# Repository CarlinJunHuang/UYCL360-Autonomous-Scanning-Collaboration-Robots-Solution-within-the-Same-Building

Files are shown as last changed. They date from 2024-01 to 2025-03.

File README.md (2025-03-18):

# Autonomous Scanning Collaboration Solution within the Same Building

## SDIM Group 3 - Fall 2023 at Southern University of Science and Technology

We are Group 3 from the School of System Design and Intelligent Manufacturing (SDIM) during the Fall 2023 semester at Southern University of Science and Technology. We have proposed an autonomous scanning solution designed for collaborative operation within the same building. This solution is aimed at alleviating the physical labor burden of technical workers in construction site measurement and quantification tasks.

### Design and Functionality

Explore more on my personal website: https://huangjuncarlin.me/hero-works/uycl360

In terms of appearance, we have conducted Kansei Engineering measurements and established engineering features to create a design that meets the enterprise's demands for a sense of technology and reliability. Functionally, we have broken down the requirements into four aspects: movement, scanning, scheduling, and management. We have implemented various technical solutions, including:

- A screw rail scanner lifting mechanism
- Ultra-wideband wireless communication for centimeter-level machine positioning
- UWB feedback control for following the operator's movement
- Dual-loop motion control with PID for speed and position
- Part simulation and optimization using Abaqus
- APP and physical controller design compliant with ergonomics

For a detailed overview, please refer to our key selling points image below:
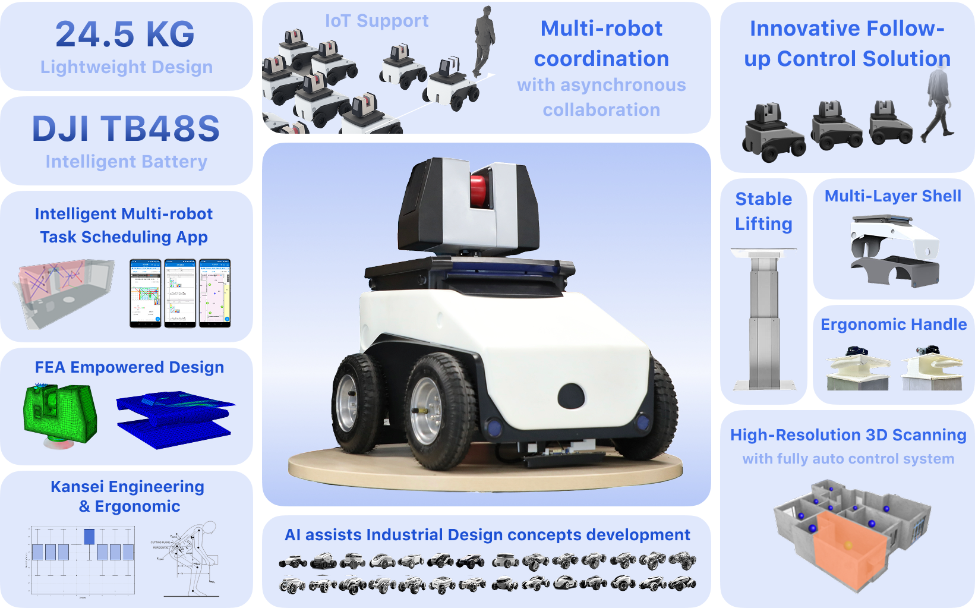
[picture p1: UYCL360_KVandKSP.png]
Key Selling Points


### Open Source Commitment

We are committed to open-sourcing as many of the technologies and techniques we have applied as possible, with the hope of aiding your learning journey. 
However, please note that some documentation may involve third-party commercial copyrights, and we will upload such material after proper anonymization and consideration.

By the way, in most cases our source text or files in this repository are in Chinese. But we will try our best to translate those parts into English via DeepL or Google Translate.

### How You Can Contribute

If you find this useful, please give us a Star or let us know! Should you have any questions, feel free to ask us.

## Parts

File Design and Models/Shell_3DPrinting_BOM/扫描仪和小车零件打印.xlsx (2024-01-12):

扫描仪+小车车壳 打样需求
序号 | 物料名称（STL文件名） | 图片 | 数量 | 样色
1 | 扫描仪-最左侧黑壳.STL |  | 1
2 | 扫描仪-左中侧灰壳.STL |  | 1
3 | 扫描仪-中间黑-红-黑部件.STL |  | 1
4 | 扫描仪-右中侧灰壳.STL |  | 1
5 | 扫描仪-最右侧黑壳.STL |  | 1
6 | 小车-外壳顶.STL |  | 1
7 | 小车-外壳中.STL |  | 1
8 | 小车-外壳底.STL |  | 1

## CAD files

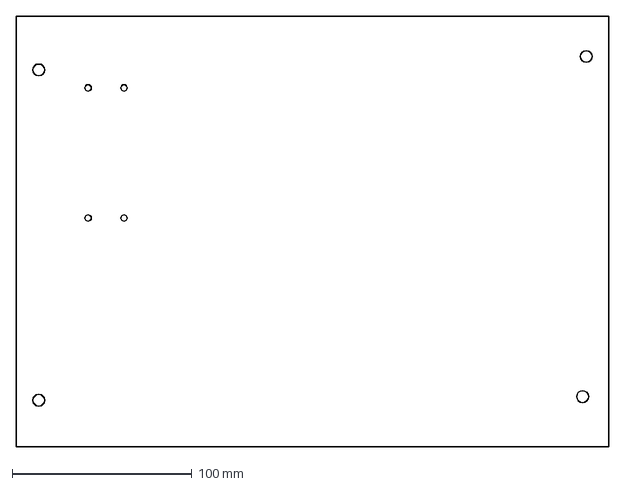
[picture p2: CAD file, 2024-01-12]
Chassis basics/Chassis Model/板V3.DXF
330.0 x 240.0 mm

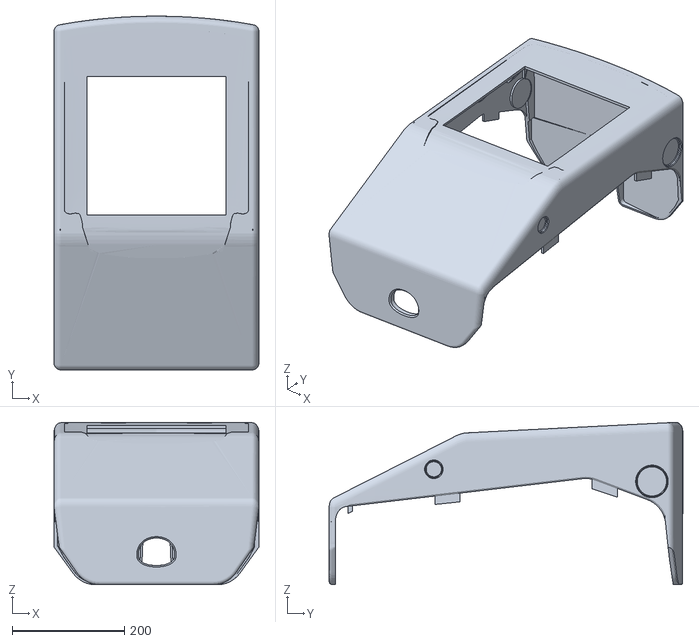
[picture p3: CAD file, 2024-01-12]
Design and Models/Shell_3DPrinting_BOM/小车-外壳中.STL
365.1 x 629.9 x 289.3

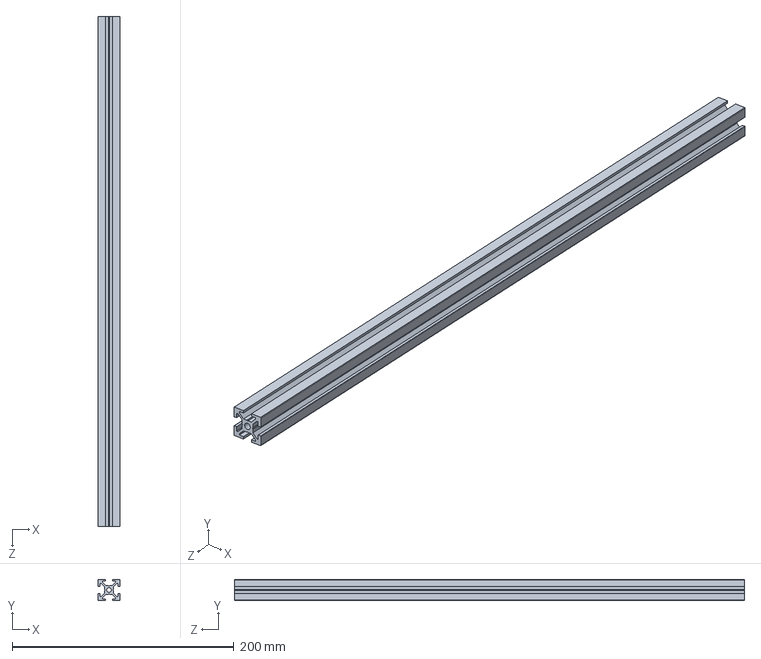
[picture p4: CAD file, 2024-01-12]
Chassis basics/Chassis Model/底盘横梁（4根）.SLDPRT
20.0 x 19.2 x 460.0 mm

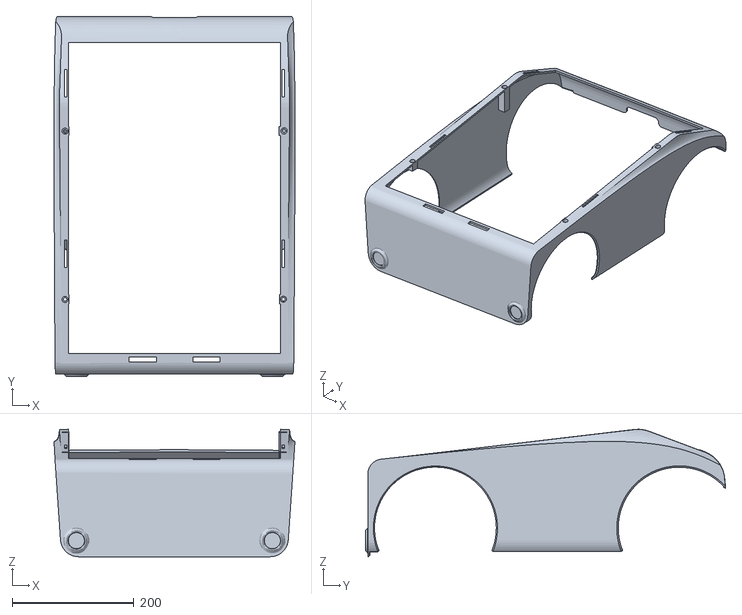
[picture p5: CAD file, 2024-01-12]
Design and Models/Shell_3DPrinting_BOM/小车-外壳底.STL
395.9 x 591.9 x 209.5

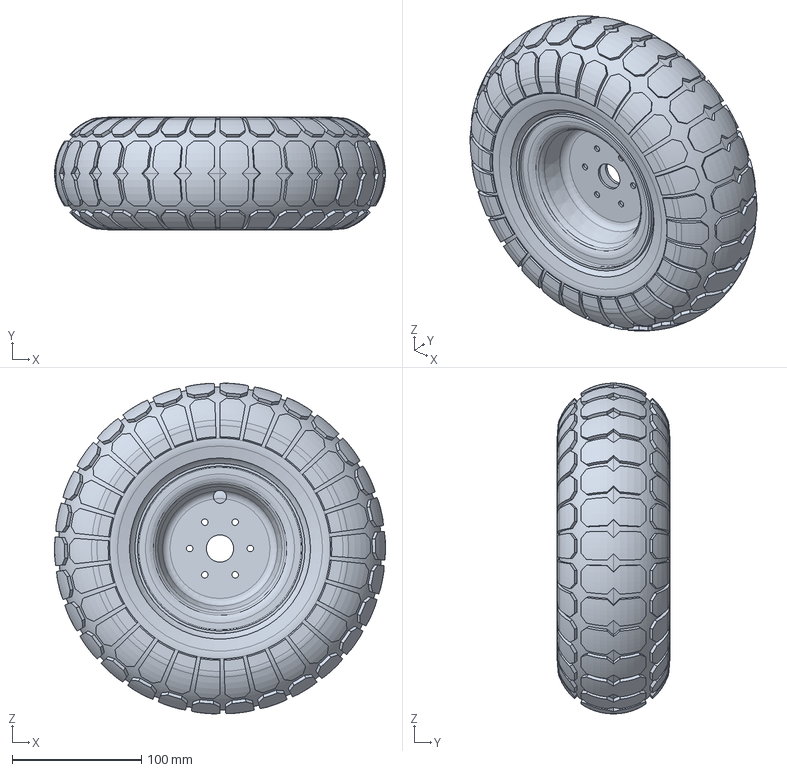
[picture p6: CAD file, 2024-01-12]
Chassis basics/Chassis Model/充气轮_10寸(直径256mm）.stp
256.0 x 87.1 x 255.8 mm

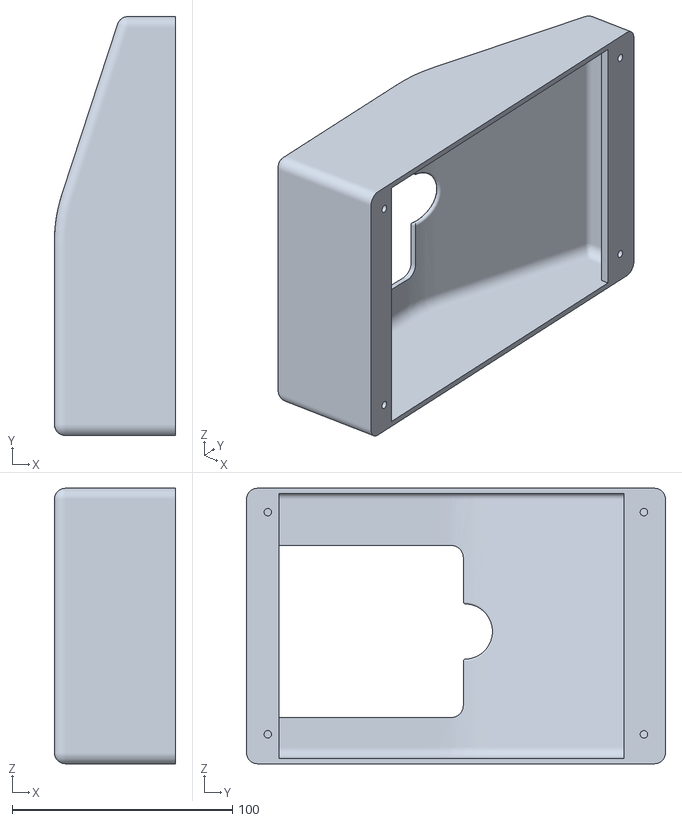
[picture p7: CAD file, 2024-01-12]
Design and Models/Shell_3DPrinting_BOM/扫描仪-最左侧黑壳.STL
55.0 x 190.0 x 125.0

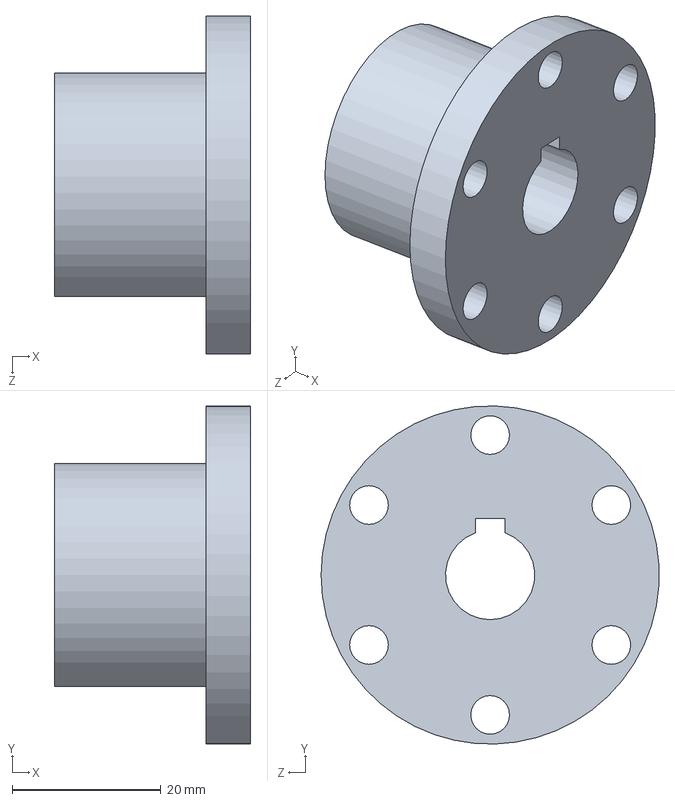
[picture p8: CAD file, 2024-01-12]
Chassis basics/Chassis Model/轮胎联轴器.SLDPRT
26.4 x 45.4 x 45.4 mm

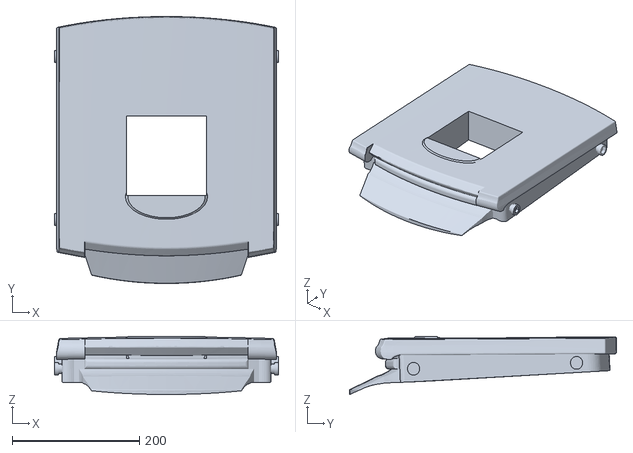
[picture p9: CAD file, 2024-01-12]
Design and Models/Shell_3DPrinting_BOM/小车-外壳顶.STL
352.1 x 419.5 x 91.2

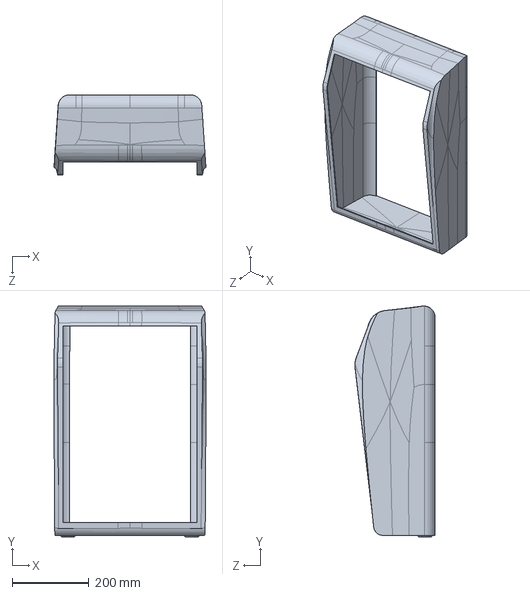
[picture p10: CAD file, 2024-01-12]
Chassis basics/Chassis Model/不知道该不该死10底.SLDPRT
395.9 x 601.8 x 209.5 mm

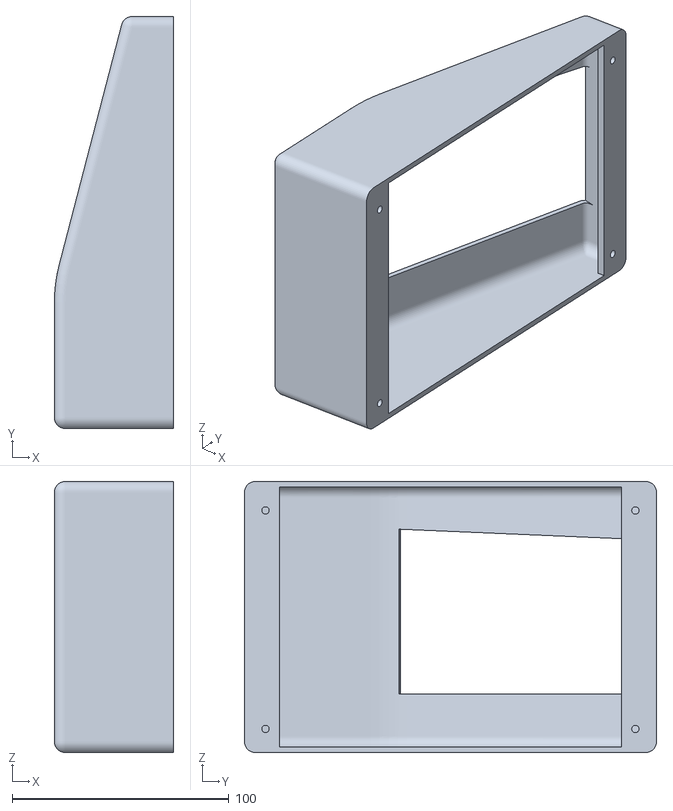
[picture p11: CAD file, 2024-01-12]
Design and Models/Shell_3DPrinting_BOM/扫描仪-最右侧黑壳.STL
55.0 x 190.0 x 125.0

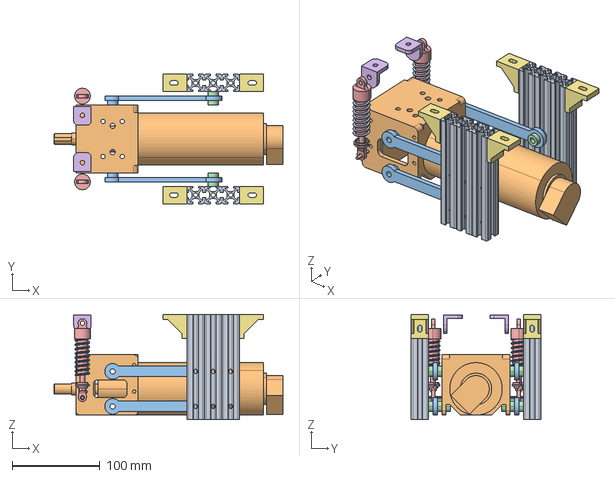
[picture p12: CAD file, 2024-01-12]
Chassis basics/Chassis Model/MD60独立悬挂.stp
261.5 x 148.0 x 120.0 mm

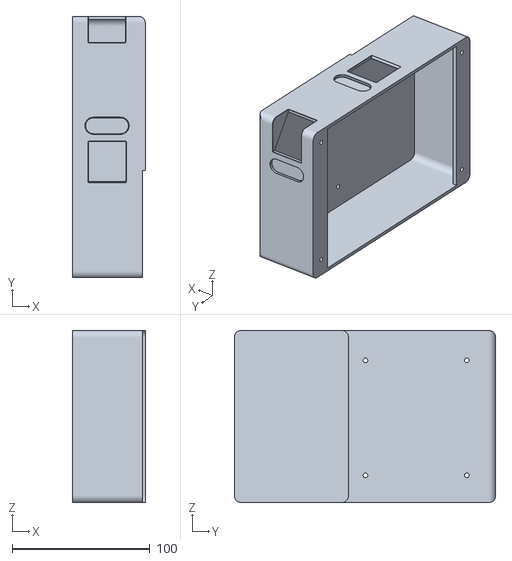
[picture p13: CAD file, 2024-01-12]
Design and Models/Shell_3DPrinting_BOM/扫描仪-左中侧灰壳.STL
52.9 x 190.0 x 125.0

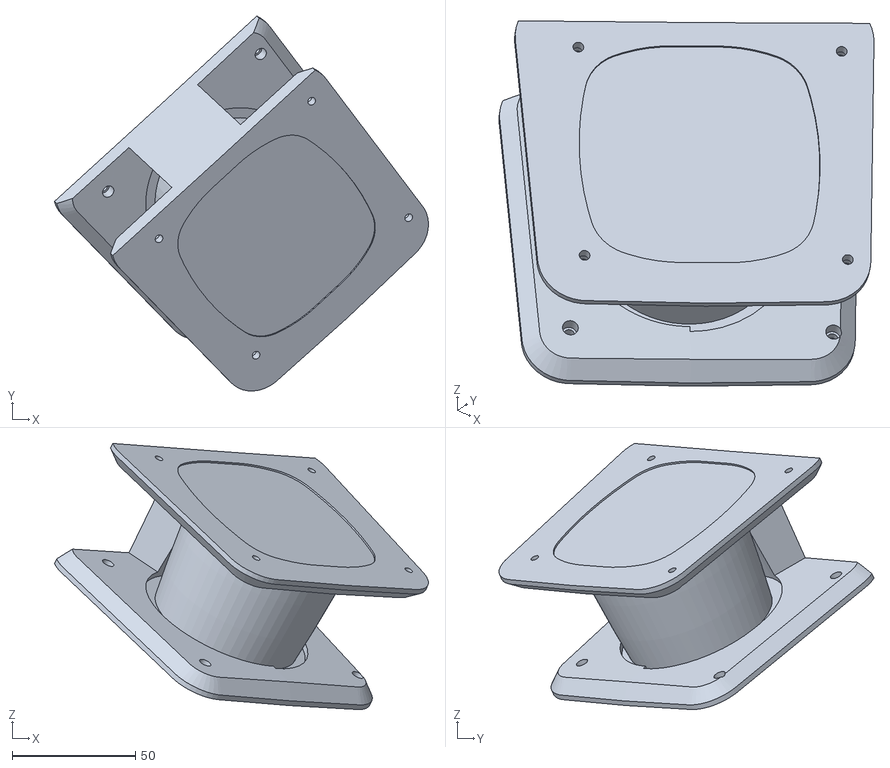
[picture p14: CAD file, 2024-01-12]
Design and Models/Shell_3DPrinting_BOM/扫描仪-中间黑-红-黑部件.STL
151.9 x 152.3 x 108.1

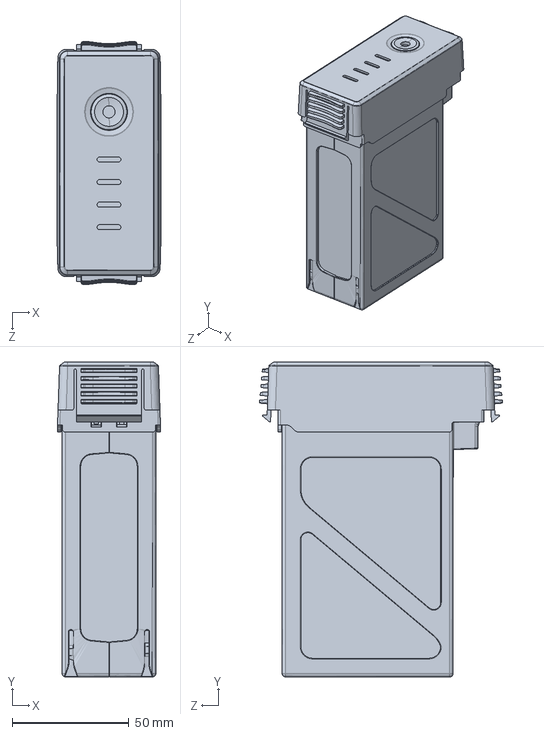
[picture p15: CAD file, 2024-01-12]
Chassis basics/Chassis Model/TB47S电池官网.SLDPRT
44.3 x 134.8 x 103.9 mm

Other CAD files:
Chassis basics/Chassis Model/2020型材截面.SLDPRT
Design and Models/Shell_3DPrinting_BOM/扫描仪-右中侧灰壳.STL
Chassis basics/Chassis Model/型材截面2020.dxf
Chassis basics/Chassis Model/板V1.SLDPRT
Chassis basics/Chassis Model/MD60轮组模块.stp
Chassis basics/Chassis Model/_MD60________^MD60独立悬挂.stp.SLDPRT
Chassis basics/Chassis Model/底盘纵梁（2根）.SLDPRT
Chassis basics/Chassis Model/板V1.DXF
Chassis basics/Chassis Model/板V2.DXF

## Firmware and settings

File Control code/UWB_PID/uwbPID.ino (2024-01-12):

//#include <SimpleKalmanFilter.h>

#define LED PC13                    //调试用的LED

//以下为左前方电机引脚定义
#define LF_Motor_IN1 PA5            //LF电机使能引脚1
#define LF_Motor_IN2 PA4            //LF电机使能引脚2
#define LF_PWM PA0                  //LF电机调速引脚
#define LF_ENCODER_A PB6            //LF编码器A相引脚
#define LF_ENCODER_B PB7            //LF编码器B相引脚

//以下为右前方电机引脚定义
#define RF_Motor_IN1 PB0            //RF电机使能引脚1
#define RF_Motor_IN2 PB1            //RF电机使能引脚2
#define RF_PWM PA2                  //RF电机调速引脚
#define RF_ENCODER_A PB13           //RF编码器A相引脚
#define RF_ENCODER_B PB12           //RF编码器B相引脚

//以下为左后方电机引脚定义
#define LR_Motor_IN1 PA7            //LR电机使能引脚1
#define LR_Motor_IN2 PA6            //LR电机使能引脚2
#define LR_PWM PA1                  //LR电机调速引脚
#define LR_ENCODER_A PB8           //LR编码器A相引脚
#define LR_ENCODER_B PB9           //LR编码器B相引脚

//以下为右后电机引脚定义
#define RR_Motor_IN1 PC8           //RR电机使能引脚1
#define RR_Motor_IN2 PC9           //RR电机使能引脚2
#define RR_PWM PA3                  //RR电机调速引脚
#define RR_ENCODER_A PB15           //RR编码器A相引脚
#define RR_ENCODER_B PB14           //RR编码器B相引脚
volatile int i, m, n, position[3];
volatile float f;  //调试用的公共变量
unsigned long nowtime = 0;  //时间
const long onesecond = 1000;

int speedall = -30;
int speedchange = 0;

const int N = 4;  // 滑动窗口大小
int Height2Buffer[N];
int Height1Buffer[N];
int bufferIndex = 0;

// 增量式PID控制变量
float lastError = 0.0; // 上一次的误差
float prevError = 0.0; // 上上次的误差
float lastOutput = 0.0; // 上一次的PID输出

int lastAvgHeight2 = 300;  // 初始平均角度
int lastAvgHeight1 = 300; // 初始平均高度
const int MAX_Height2_CHANGE = 300; // 角度变化阈值
const int MAX_Height1_CHANGE = 300; // 高度变化阈值

int Height2_int = 0, Height1_int = 0, Height_Bias = 0;
float Height2 = 0, filteredHeight2 = 0, filteredHeight1 = 0;
//SimpleKalmanFilter kalmanHeight2(10.0, 0.1, 0.01); // 这些值需要您根据实际情况调整
//SimpleKalmanFilter kalmanHeight1(10.0, 0.1, 0.01); // e_mea, e_est, q


volatile int LF_Velocity = 0, LF_Count = 0;  //左前方电机编码器，Count计数变量 Velocity存储设定时间内A相下降沿的个数，与实际转速正相关
volatile int RF_Velocity = 0, RF_Count = 0;  //左后方电机编码器，Count计数变量 Velocity存储设定时间内A相下降沿的个数，与实际转速正相关
volatile int LR_Velocity = 0, LR_Count = 0;  //右前方电机编码器，Count计数变量 Velocity存储设定时间内A相下降沿的个数，与实际转速正相关
volatile int RR_Velocity = 0, RR_Count = 0;  //右后方电机编码器，Count计数变量 Velocity存储设定时间内A相下降沿的个数，与实际转速正相关

String Target_Value;                                                        //串口获取的速度字符串变量
volatile byte Patrol_data[5] = {41, 42, 43};
volatile int LF_value, RF_value, LR_value, RR_value;                        //用于存储通过PI控制器计算得到的用于调整电机转速的PWM值，最大值65535
float K_p = 0.4, K_i = 0.001, K_d = 0.0015; // 微分系数
float PID_Restrict = 85.0; // PID输出限制
float integral = 0.0; // 积分项
//float lastError = 0.0; // 上一次的误差
float KP = 175, KI = 20;                                                    //PI参数，此处调整会影响启动电流，低速时可能引起震荡
volatile float LF_Target = 0, RF_Target = 0, LR_Target = 0, RR_Target = 0;  //电机转速目标值,5ms定时器最大可用范围±280，2ms定时器，最大可用范围±120

///*********** 限幅************
//  以下两个参数让输出的PWM在一个合理区间
//  当输出的PWM小于1500时电机不转 所以要设置一个启始PWM
//  STM32单片机的PWM不能超过65535 所以 PWM_Restrict 起到限制上限的作用
//*****************************/
int startPWM = 1500;       //克服死区的启始PWM
int PWM_Restrict = 64000;  //startPW+PWM_Restric=65500<65535

/**********外部中断触发计数器函数（4个电机需要独立的外部中断处理函数）************
  根据转速的方向不同我们将计数器累计为正值或者负值(计数器累计为正值为负值为计数器方向)
  只有方向累计正确了才可以实现正确的调整,否则会出现逆方向满速旋转
  ※※※※※※超级重点※※※※※※
  所谓累计在正确的方向即
  (1)计数器方向
  (2)电机输出方向(控制电机转速方向的接线是正着接还是反着接)
  (3)PI 控制器 里面的误差(Basi)运算是目标值减当前值(Target-Encoder),还是当前值减目标值(Encoder-Target)
  三个方向只有对应上才会有效果否则你接上就是使劲的朝着一个方向(一般来说是反方向)满速旋转，出现这种问题，需要将AB相的线调过来，或改下引脚定义
  我例子里是我自己对应好的,如果其他驱动单片机在自己尝试的时候出现满速旋转就是三个方向没对应上
  下列函数中由于在A相上升沿触发时,B相是低电平,和A相下降沿触发时B是高电平是一个方向,在这种触发方式下,我们将count累计为正,另一种情况将count累计为负
********************************************/
void LF_READ_ENCODER_A()  //左前方电机A相中断
{
  if (digitalRead(LF_ENCODER_A) == HIGH) {
    if (digitalRead(LF_ENCODER_B) == LOW)
      LF_Count++;  //根据另外一相电平判定方向
    else
      LF_Count--;
  } else {
    if (digitalRead(LF_ENCODER_B) == LOW)
      LF_Count--;  //根据另外一相电平判定方向
    else
      LF_Count++;
  }
}
void RF_READ_ENCODER_A()  //右前方电机A相中断
{
  if (digitalRead(RF_ENCODER_A) == HIGH) {
    if (digitalRead(RF_ENCODER_B) == LOW)
      RF_Count++;  //根据另外一相电平判定方向
    else
      RF_Count--;
  } else {
    if (digitalRead(RF_ENCODER_B) == LOW)
      RF_Count--;  //根据另外一相电平判定方向
    else
      RF_Count++;
  }
}
void LR_READ_ENCODER_A()  //左后方电机A相中断
{
  if (digitalRead(LR_ENCODER_A) == HIGH) {
    if (digitalRead(LR_ENCODER_B) == LOW)
      LR_Count++;  //根据另外一相电平判定方向
    else
      LR_Count--;
  } else {
    if (digitalRead(LR_ENCODER_B) == LOW)
      LR_Count--;  //根据另外一相电平判定方向
    else
      LR_Count++;
  }
}

void RR_READ_ENCODER_A()  //右后方电机A相中断
{
  if (digitalRead(RR_ENCODER_A) == HIGH) {
    if (digitalRead(RR_ENCODER_B) == LOW)
      RR_Count++;  //根据另外一相电平判定方向
    else
      RR_Count--;
  } else {
    if (digitalRead(RR_ENCODER_B) == LOW)
      RR_Count--;  //根据另外一相电平判定方向
    else
      RR_Count++;
  }
}
/*****位置式PID控制器*****/
int calculatePID(float targetHeight, float currentHeight) {
  float error = targetHeight - currentHeight; // 计算偏差
  integral += error; // 更新积分项
  float derivative = error - lastError; // 计算微分项
  lastError = error; // 更新上一次误差

  // 计算PID输出
  float output = K_p * error + K_i * integral + K_d * derivative;

  // 限幅
  if (output > PID_Restrict) {
    output = PID_Restrict;
  } else if (output < -PID_Restrict) {
    output = -PID_Restrict;
  }

  return output;
}

float calculateIncrementalPID(float targetHeight, float currentHeight) {
  float error = targetHeight - currentHeight; // 当前误差
  float deltaOutput = K_p * (error - lastError) // P项的变化量
                      + K_i * error // I项的变化量
                      + K_d * (error - 2 * lastError + prevError); // D项的变化量

  // 更新误差
  prevError = lastError;
  lastError = error;

  // 更新并返回PID输出
  lastOutput += deltaOutput;

  // 限幅
  if (lastOutput > PID_Restrict) {
    lastOutput = PID_Restrict;
  } else if (lastOutput < -PID_Restrict) {
    lastOutput = -PID_Restrict;
  }

  return lastOutput;
}

/***********PI控制器****************/
int LF_Incremental_PI(int LF_Encoder, float LF_Target1) {
  static float LF_Bias, LF_MPWM = 0, LF_Last_bias = 0;      //定义全局静态浮点型变量 PWM,Bias(本次偏差),Last_bias(上次偏差)
  LF_Bias = LF_Target1 - LF_Encoder;                        //计算偏差,目标值减去当前值
  LF_MPWM += KP * (LF_Bias - LF_Last_bias) + KI * LF_Bias;  //增量式PI控制计算
  if (LF_MPWM > PWM_Restrict)
    LF_MPWM = PWM_Restrict;  //限幅
  if (LF_MPWM < -PWM_Restrict)
    LF_MPWM = -PWM_Restrict;  //限幅
  LF_Last_bias = LF_Bias;     //保存上一次偏差
  return LF_MPWM;             //增量输出
}
int RF_Incremental_PI(int RF_Encoder, float RF_Target1) {
  static float RF_Bias, RF_MPWM = 0, RF_Last_bias = 0;      //定义全局静态浮点型变量 PWM,Bias(本次偏差),Last_bias(上次偏差)
  RF_Bias = RF_Target1 - RF_Encoder;                        //计算偏差,目标值减去当前值
  RF_MPWM += KP * (RF_Bias - RF_Last_bias) + KI * RF_Bias;  //增量式PI控制计算
  if (RF_MPWM > PWM_Restrict)
    RF_MPWM = PWM_Restrict;  //限幅
  if (RF_MPWM < -PWM_Restrict)
    RF_MPWM = -PWM_Restrict;  //限幅
  RF_Last_bias = RF_Bias;     //保存上一次偏差
  return RF_MPWM;             //增量输出
}
int LR_Incremental_PI(int LR_Encoder, float LR_Target1) {
  static float LR_Bias, LR_MPWM = 0, LR_Last_bias = 0;      //定义全局静态浮点型变量 PWM,Bias(本次偏差),Last_bias(上次偏差)
  LR_Bias = LR_Target1 - LR_Encoder;                        //计算偏差,目标值减去当前值
  LR_MPWM += KP * (LR_Bias - LR_Last_bias) + KI * LR_Bias;  //增量式PI控制计算
  if (LR_MPWM > PWM_Restrict)
    LR_MPWM = PWM_Restrict;  //限幅
  if (LR_MPWM < -PWM_Restrict)
    LR_MPWM = -PWM_Restrict;  //限幅
  LR_Last_bias = LR_Bias;     //保存上一次偏差
  return LR_MPWM;             //增量输出
}
int RR_Incremental_PI(int RR_Encoder, float RR_Target1) {
  static float RR_Bias, RR_MPWM = 0, RR_Last_bias = 0;      //定义全局静态浮点型变量 PWM,Bias(本次偏差),Last_bias(上次偏差)
  RR_Bias = RR_Target1 - RR_Encoder;                        //计算偏差,目标值减去当前值
  RR_MPWM += KP * (RR_Bias - RR_Last_bias) + KI * RR_Bias;  //增量式PI控制计算
  if (RR_MPWM > PWM_Restrict)
    RR_MPWM = PWM_Restrict;  //限幅
  if (RR_MPWM < -PWM_Restrict)
    RR_MPWM = -PWM_Restrict;  //限幅
  RR_Last_bias = RR_Bias;     //保存上一次偏差
  return RR_MPWM;             //增量输出
}

/**********电机驱动函数*********/
void LF_Set_PWM(int LF_motora) {
  if (LF_motora > 0)  //如果算出的PWM为正
  {

    digitalWrite(LF_Motor_IN1, 1);
    digitalWrite(LF_Motor_IN2, 0);
    pwmWrite(LF_PWM, LF_motora + startPWM);  //让PWM在设定正转方向(我们认为的正转方向)正向输出调整，此处的PWM输出函数跟Mega2560不同
  } else if (LF_motora == 0)                 //如果PWM为0停车
  {
    digitalWrite(LF_Motor_IN2, 0);
    digitalWrite(LF_Motor_IN1, 0);
  } else if (LF_motora < 0)  //如果算出的PWM为负
  {

    digitalWrite(LF_Motor_IN1, 0);
    digitalWrite(LF_Motor_IN2, 1);
    pwmWrite(LF_PWM, -LF_motora + startPWM);  //让PWM在设定反转方向反向输出调整
  }
}
void RF_Set_PWM(int RF_motora) {
  if (RF_motora > 0)  //如果算出的PWM为正
  {

    digitalWrite(RF_Motor_IN1, 1);
    digitalWrite(RF_Motor_IN2, 0);
    pwmWrite(RF_PWM, RF_motora + startPWM);  //让PWM在设定正转方向(我们认为的正转方向)正向输出调整
  } else if (RF_motora == 0)                 //如果PWM为0停车
  {
    digitalWrite(RF_Motor_IN2, 0);
    digitalWrite(RF_Motor_IN1, 0);
  } else if (RF_motora < 0)  //如果算出的PWM为负
  {

    digitalWrite(RF_Motor_IN1, 0);
    digitalWrite(RF_Motor_IN2, 1);
    pwmWrite(RF_PWM, -RF_motora + startPWM);  //让PWM在设定反转方向反向输出调整
  }
}
void LR_Set_PWM(int LR_motora) {
  if (LR_motora > 0)  //如果算出的PWM为正
  {

    digitalWrite(LR_Motor_IN1, 1);
    digitalWrite(LR_Motor_IN2, 0);
    pwmWrite(LR_PWM, LR_motora + startPWM);  //让PWM在设定正转方向(我们认为的正转方向)正向输出调整
  } else if (LR_motora == 0)                 //如果PWM为0停车
  {
    digitalWrite(LR_Motor_IN2, 0);
    digitalWrite(LR_Motor_IN1, 0);
  } else if (LR_motora < 0)  //如果算出的PWM为负
  {

    digitalWrite(LR_Motor_IN1, 0);
    digitalWrite(LR_Motor_IN2, 1);
    pwmWrite(LR_PWM, -LR_motora + startPWM);  //让PWM在设定反转方向反向输出调整
  }
}
void RR_Set_PWM(int RR_motora) {
  if (RR_motora > 0)  //如果算出的PWM为正
  {

    digitalWrite(RR_Motor_IN1, 1);
    digitalWrite(RR_Motor_IN2, 0);
    pwmWrite(RR_PWM, RR_motora + startPWM);  //让PWM在设定正转方向(我们认为的正转方向)正向输出调整
  } else if (RR_motora == 0)                 //如果PWM为0停车
  {
    digitalWrite(RR_Motor_IN2, 0);
    digitalWrite(RR_Motor_IN1, 0);
  } else if (RR_motora < 0)  //如果算出的PWM为负
  {

    digitalWrite(RR_Motor_IN1, 0);
    digitalWrite(RR_Motor_IN2, 1);
    pwmWrite(RR_PWM, -RR_motora + startPWM);  //让PWM在设定反转方向反向输出调整
  }
}
/**********定时器中断触发函数（）*********/
HardwareTimer time3(3);  //声明使用3号定时器，电机控制闭环
HardwareTimer time1(1);  //声明使用1号定时器，位置控制滨海

void control() {   //3号定时中断
  //  cli();    //关闭所有中断，此处尝试不加也行
  //把采用周期(内部定时中断周期)所累计的脉冲下降沿的个数,赋值给速度
  LF_Velocity = LF_Count;
  RF_Velocity = RF_Count;
  LR_Velocity = LR_Count;
  RR_Velocity = RR_Count;

  //脉冲计数器清零
  LF_Count = 0;
  RF_Count = 0;
  LR_Count = 0;
  RR_Count = 0;

  //以下为4个电机同时计算PID参数
  LF_value = LF_Incremental_PI(LF_Velocity, LF_Target);  //通过目标值和当前值在PID函数下算出我们需要调整用的PWM值
  RF_value = RF_Incremental_PI(RF_Velocity, RF_Target);
  LR_value = LR_Incremental_PI(LR_Velocity, LR_Target);
  RR_value = RR_Incremental_PI(RR_Velocity, RR_Target);
  //以下为4个电机同时输出PWM值
  LF_Set_PWM(LF_value);
  RF_Set_PWM(RF_value);
  LR_Set_PWM(LR_value);
  RR_Set_PWM(RR_value);

  //以下为调试代码，调试完成需要删除，避免浪费CPU资源

  // Serial1.print(LF_value);  //输出左前轮的PWM值
  // Serial.print(",");
  // Serial1.println(LF_Velocity);  //输出左前轮的转速
  //  sei();     //打开所有中断，此处尝试不加也行
}

void patrol() {  //1号定时中断
  static byte lastByte = 0; // 用于存储上一个字节
  static byte receivedData[4];
  static int dataIndex = 0; // 数据索引
  bool dataReady = false; // 数据是否准备好的标志

  while (Serial1.available()) {
    byte currentByte = Serial1.read();

    // 检查是否找到了帧结束标志 \r\n
    if (lastByte == '\r' && currentByte == '\n') {
      // 如果已经收集了4个字节的数据，那么标记数据已准备好
      if (dataIndex == 4) {
        dataReady = true;
      }
      dataIndex = 0; // 重置数据索引，无论数据是否完整
    } else if (dataIndex < 4) {
      // 收集数据
      receivedData[dataIndex++] = currentByte;
    }

    // 更新上一个字节
    lastByte = currentByte;

    if (dataReady) {
      Height1_int = (receivedData[0] << 8) | receivedData[1];
      Height2_int = (receivedData[2] << 8) | receivedData[3];
      Height2_int = Height2_int - 8;

      //
      //      Serial.print(Height2_int); Serial.print(",");
      //      Serial.print(Height1_int); Serial.print(",");

      // 检测异常值并处理
      if (abs(Height2_int - lastAvgHeight2) > MAX_Height2_CHANGE) {
        Height2_int = 100;
      }
      if (abs(Height1_int - lastAvgHeight1) > MAX_Height1_CHANGE) {
        Height1_int = 100;
      }

      // 更新缓冲区
      Height2Buffer[bufferIndex] = Height2_int;
      Height1Buffer[bufferIndex] = Height1_int;
      bufferIndex = (bufferIndex + 1) % N;

      // 计算滑动平均
      int avgHeight2 = 0, avgHeight1 = 0;
      for (int i = 0; i < N; i++) {
        avgHeight2 += Height2Buffer[i];
        avgHeight1 += Height1Buffer[i];
      }
      avgHeight2 /= N;
      avgHeight1 /= N;

      // 更新上一个平均值
      lastAvgHeight2 = avgHeight2;
      lastAvgHeight1 = avgHeight1;

      // 打印实验数据
      //      Serial.print(speedall); Serial.print(",");
      //      Serial.println(avgHeight1);

      int R_PID = calculateIncrementalPID(0, Height2_int - 100);
      int L_PID = calculateIncrementalPID(0, Height1_int - 100);

      int tempdiff = (Height1_int - Height2_int) * 3 / 4;

      LF_Target = L_PID - tempdiff;
      RF_Target = R_PID + tempdiff;
      LR_Target = L_PID - tempdiff;
      RR_Target = R_PID + tempdiff;

      Serial.print(avgHeight1); Serial.print(",");
      Serial.println(avgHeight2);
      //      Serial.println(LF_Target);

      dataReady = false; // 重置数据准备标志
    }

  }
}


void setup()
{
  delay(1000);
  Serial1.begin(115200);  //打开串口1，PA9、PA10，用于控制和反馈信息传输
  Serial3.begin(9600);  //打开串口3，PB10、PB11，用于与位置传感器通讯
  memset(Height2Buffer, 0, sizeof(Height2Buffer)); // 初始化缓冲区
  memset(Height1Buffer, 0, sizeof(Height1Buffer));


  pinMode(LED, OUTPUT);  //调试用的闪烁LED

  { //初始化4个电机的控制和反馈引脚
    pinMode(LF_ENCODER_A, INPUT);  //设置两个相线为输入模式
    pinMode(LF_ENCODER_B, INPUT);
    pinMode(LF_Motor_IN1, OUTPUT_OPEN_DRAIN);  //设置两个驱动引脚为输出模式，由于stm32的引脚接收5V作为输出时需要工作在开漏输出模式下，这与Mega2560函数定义是有差别的，Mega2560可以直接推挽输出5V，引脚直接配置为OUTPUT即可
    pinMode(LF_Motor_IN2, OUTPUT_OPEN_DRAIN);
    pinMode(LF_PWM, PWM_OPEN_DRAIN);

    pinMode(RF_ENCODER_A, INPUT);  //设置两个相线为输入模式
    pinMode(RF_ENCODER_B, INPUT);
    pinMode(RF_Motor_IN1, OUTPUT_OPEN_DRAIN);  //设置两个驱动引脚为输出模式，由于stm32的引脚接收5V作为输出时需要工作在开漏输出模式下，这与Mega2560函数定义是有差别的，Mega2560可以直接推挽输出5V，引脚直接配置为OUTPUT即可
    pinMode(RF_Motor_IN2, OUTPUT_OPEN_DRAIN);
    pinMode(RF_PWM, PWM_OPEN_DRAIN);

    pinMode(LR_ENCODER_A, INPUT);  //设置两个相线为输入模式
    pinMode(LR_ENCODER_B, INPUT);
    pinMode(LR_Motor_IN1, OUTPUT_OPEN_DRAIN);  //设置两个驱动引脚为输出模式，由于stm32的引脚接收5V作为输出时需要工作在开漏输出模式下，这与Mega2560函数定义是有差别的，Mega2560可以直接推挽输出5V，引脚直接配置为OUTPUT即可
    pinMode(LR_Motor_IN2, OUTPUT_OPEN_DRAIN);
    pinMode(LR_PWM, PWM_OPEN_DRAIN);

    pinMode(RR_ENCODER_A, INPUT);  //设置两个相线为输入模式
    pinMode(RR_ENCODER_B, INPUT);
    pinMode(RR_Motor_IN1, OUTPUT_OPEN_DRAIN);  //设置两个驱动引脚为输出模式，由于stm32的引脚接收5V作为输出时需要工作在开漏输出模式下，这与Mega2560函数定义是有差别的，Mega2560可以直接推挽输出5V，引脚直接配置为OUTPUT即可
    pinMode(RR_Motor_IN2, OUTPUT_OPEN_DRAIN);
    pinMode(RR_PWM, PWM_OPEN_DRAIN);
  }
  //下面是外部中断的初始化
  attachInterrupt(LF_ENCODER_A, LF_READ_ENCODER_A, FALLING);  //开启对应A相引脚的外部中断,触发方式为FALLING 即下降沿都触发,触发的中断函数为 LF_ENCODER_A
  attachInterrupt(RF_ENCODER_A, RF_READ_ENCODER_A, FALLING);
  attachInterrupt(LR_ENCODER_A, LR_READ_ENCODER_A, FALLING);
  attachInterrupt(RR_ENCODER_A, RR_READ_ENCODER_A, FALLING);

  Serial.setTimeout(10);

  //下面是3号定时器（电机速度闭环）的初始化，Mega2560的用法与此处有差异，参考引用库函数才行
  time3.pause();                                   // Pause the timer while we're configuring it
  time3.setPeriod(5000);                           // Set up period in microseconds，5000us=5ms
  time3.setMode(TIMER_CH3, TIMER_OUTPUT_COMPARE);  // Set up an interrupt on channel 1
  time3.setCompare(TIMER_CH3, 1);                  // Interrupt 3 count after each update
  time3.attachInterrupt(3, control);               //定时中断函数名声明

  //下面是1号定时器（位置闭环）的初始化，Mega2560的用法与此处有差异，参考引用库函数才行
  time1.pause();                                   // Pause the timer while we're configuring it
  time1.setPeriod(75000);                         // Set up period in microseconds，100000us=100ms
  time1.setMode(TIMER_CH1, TIMER_OUTPUT_COMPARE);  // Set up an interrupt on channel 1
  time1.setCompare(TIMER_CH1, 1);                  // Interrupt 1 count after each update
  time1.attachInterrupt(1, patrol);                //定时中断函数名声明
  //启动3号和1号定时器
  time3.refresh();                                  // Refresh the timer's count, prescale, and overflow
  time1.refresh();                                 // Refresh the timer's count, prescale, and overflow
  time3.resume();                                  // Start the timer counting
  time1.resume();                                  // Start the timer counting
}

void loop()
{

}

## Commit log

2024-01-12 Add Files and Codes V1
    Preliminarily added some Arduino side code, no explanation yet.
    [2020型材截面.SLDPRT, MD60独立悬挂.stp, MD60轮组模块.stp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]
2024-01-12 Add Shell_STL
    but still not translate or lack a explanation document
    [小车-外壳中.STL, 小车-外壳底.STL, 小车-外壳顶.STL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]
2024-01-12 Design Presentation Material
